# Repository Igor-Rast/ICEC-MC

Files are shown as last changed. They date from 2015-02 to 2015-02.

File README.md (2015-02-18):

# ICEC-MC
ICEC-MC Cape for BeagleBone Black

## Introduction
ICEC-MC is a project to create the plans, prototype board and software for a completly Open Source Motor Controller board in the form of a Cape that can be placed on a BeagleBone Black.
The ICEC-MC is build to fit the needs of the FirePick Delta Modular Tool system, Incorporating 4 Modular Tool headers. 
But should also be no problem to handle any other type of 3d printer or CNC machine.

## Project Status

Using Printipi (thanks Collin) the basic driver for moving the FirePickDelta is working. 
G1 commands are beeing performed correctly, G2 and a look ahead function are the next on the line to get fixed.
The calculations for the FirePick seems proven and i am now turning to the BBB for more pins so we can connect the neccecary for our project.
also an graphical user interface would be nice. 

+ idea  
- schematic / logic
- match pinouts
- board layout
- proto run
- debug

### Features

##### 4 endstop connection (x,y,z axis + Bed Level switch)
- configurable as opto or switch type(pull up)

##### 4 FirePick Delta EAT Modular Tool Headers ( new design +2p)
- new 18 pin header for EAT Modular Tool board to include Stepper VRef & BBB_ADC_GND 
- Old 16p EAT tool should work without problems, just dont populate the Termistor parts. ( wire differently)
 
##### 4 embedded DRV8825 stepper drivers (x,y,z,e)
- Digital Current Control (DAC088S085)
- All DRV8825 stepping modes (full step, half step, 1/4 step, 1/8 step, 1/16 step, 1/32 step).,

##### 4 steppers connection tru Modular Tool Header (one tool at a time)
- Digital Current Control (DAC088S085) (if new EAT tool used)

##### 7 BBB ADC inputs for thermistor 
- 3 on board
- 4 accessable tru Modular Tool Headers

##### 4 Servo connections 
- connect up to 4 servos or ledstrips

##### E-Stop Logic Circuit (Oh shit, Button)
- deactivate all steppers and tools with the push of a button.

##### Imbedded voltage regulators
- 12V step down --> fans , if using 24V on motors
- 5C step down --> beaglebone black and logic

##### I2C controlled standalone PWM controller (PCA9685PW)  
- 3 Enbedded Hi-Power Mosfest (AON6758) e.g. heatbed/hotend/vacuumpump
- 3 Embedded Low-Power Mosfet (NIF5002) e.g. fan/leds
- 4 PWM control of D_Out on Modular Tool Headers
- 6 PWM signals left unused (break these out?/add some status leds?)

##### 40pin Connection for Graphical Interface Expansion using cheap 4.3inch 3.2 TFT LCD modules 
- ssd1962 display driver 
- touch sensor 
- sd card reader

##### Remote on function for ATX powersupply
- turn the ATX PSU on/off using the M81/M82 (single ATX supply)

##### BBB reset button

## Developers
TODO: setup google group
If you'd like to be involved in the development of ICEC-MC, please PM me.

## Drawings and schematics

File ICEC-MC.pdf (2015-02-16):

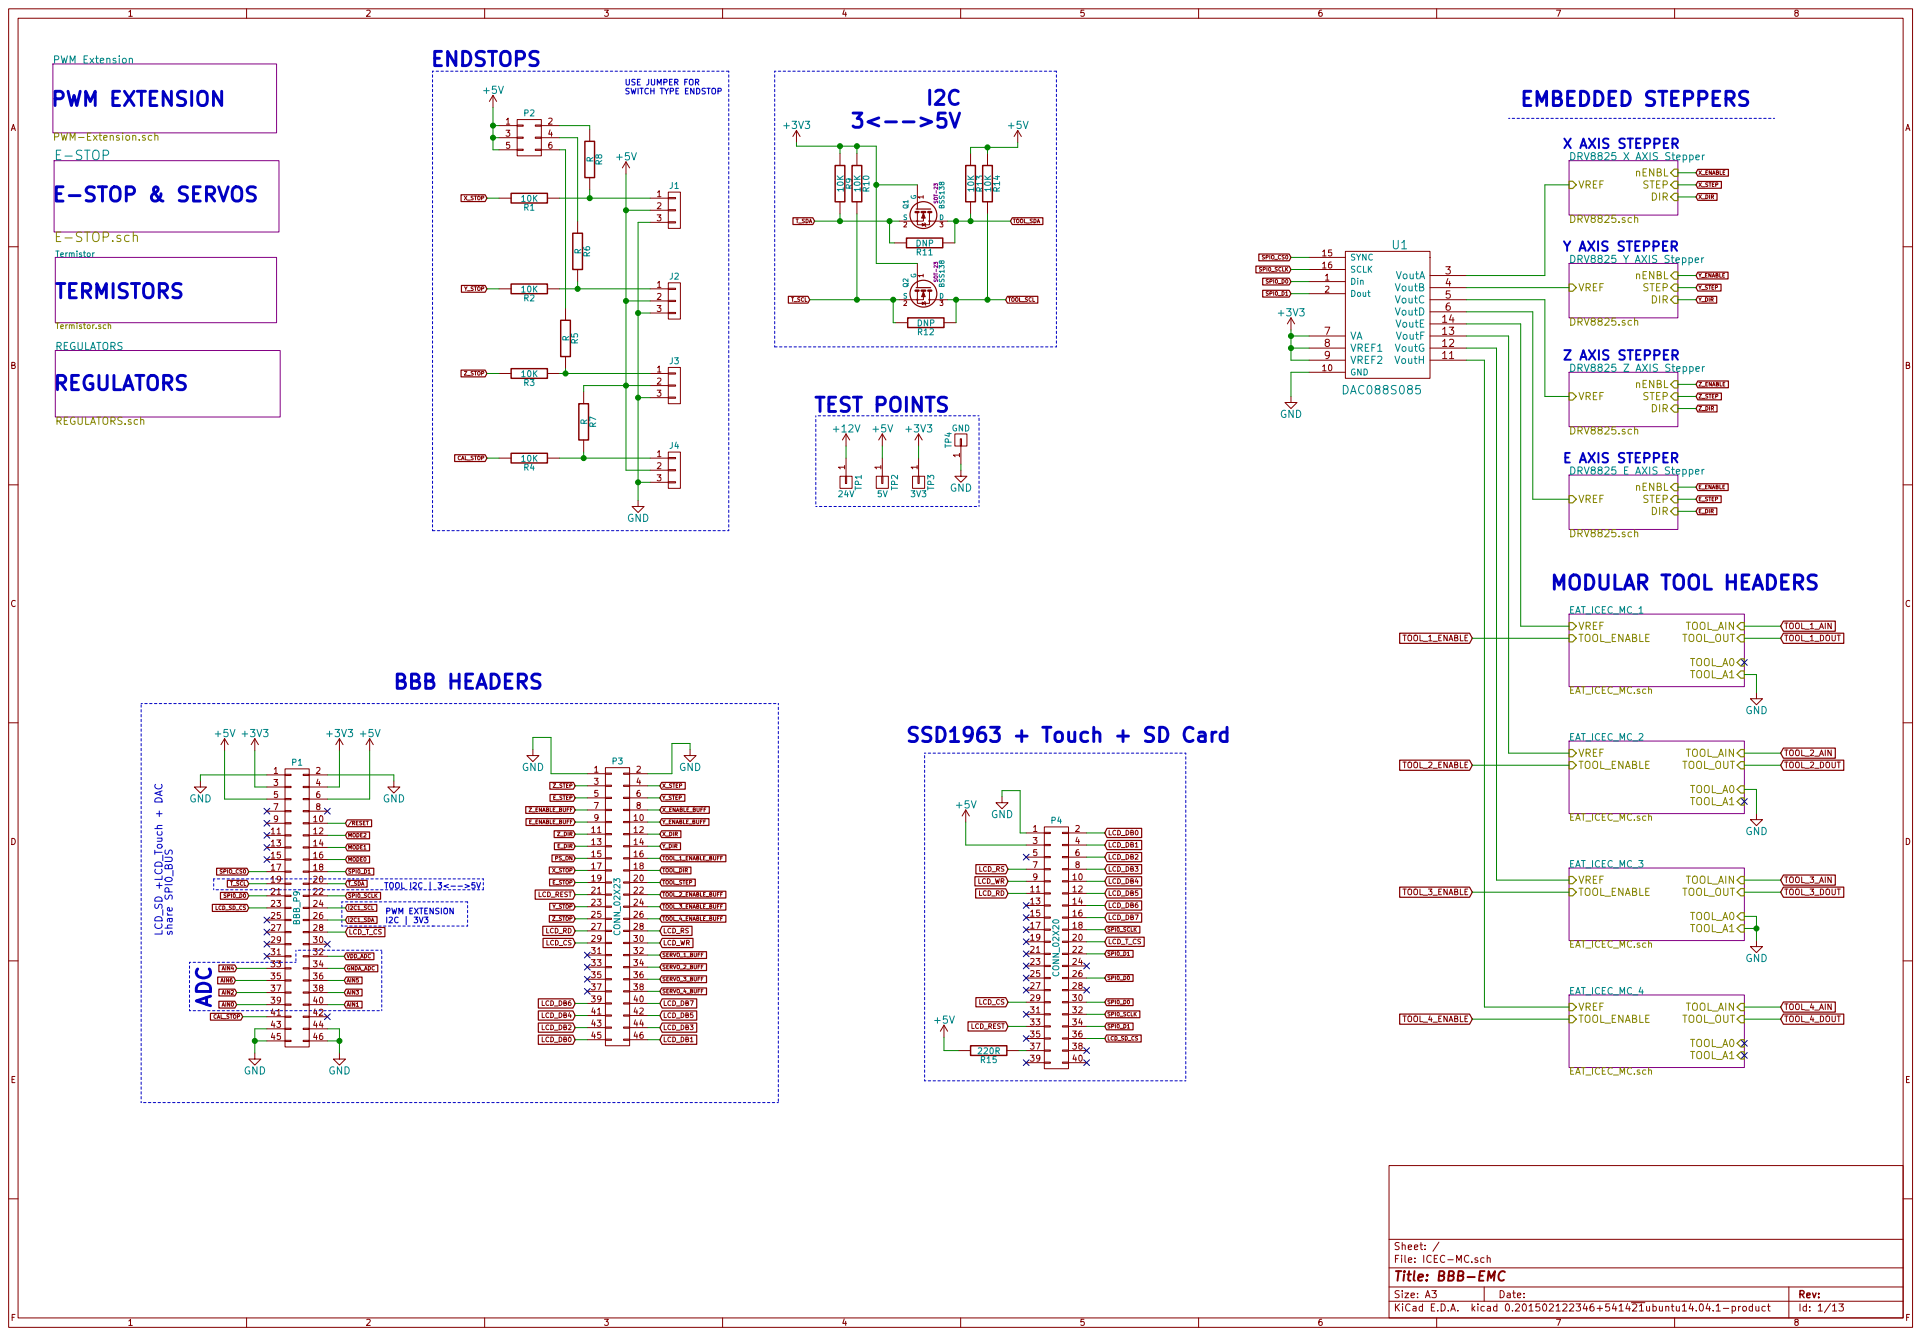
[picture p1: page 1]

PWM Extension PWM-Extension.sch

DRV8825 X AXIS Stepper DRV8825.sch STEP DIR | nENBL VREF

Y AXIS STEPPER
DRV8825 Y AXIS Stepper DRV8825.sch STEP DIR
nENBL VREF Z AXIS STEPPER

DRV8825 Z AXIS Stepper DRV8825.sch STEP DIR
nENBL VREF E AXIS STEPPER

REGULATORS

DRV8825 E AXIS Stepper DRV8825.sch STEP DIR
nENBL VREF

File: ICEC-MC.sch Sheet: /
Id: 1/13 Title: BBB-EMC

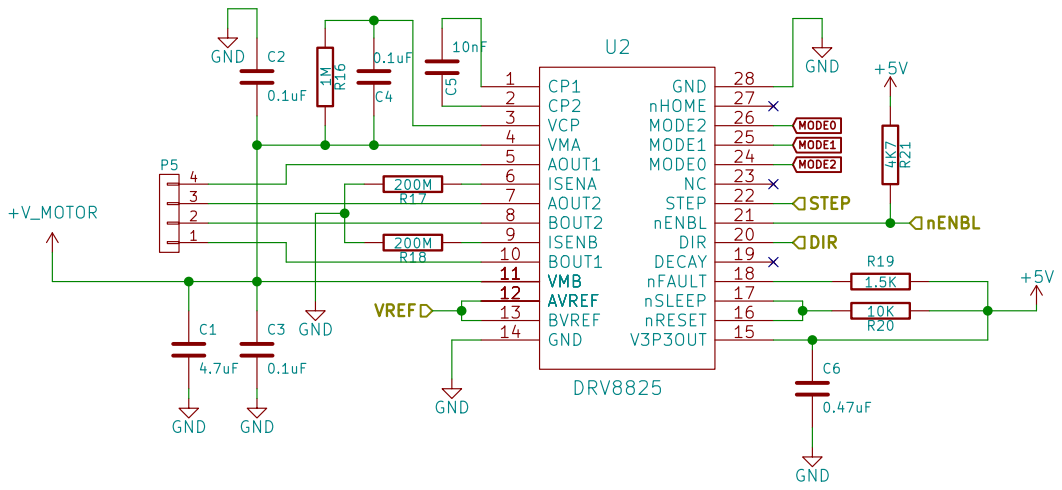
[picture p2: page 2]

MODE0 MODE1 MODE2 +V_MOTOR

File: DRV8825.sch Sheet: /DRV8825 X AXIS Stepper/
Id: 2/13 Title: DRV8825 Stepper -| ADC-->VRF

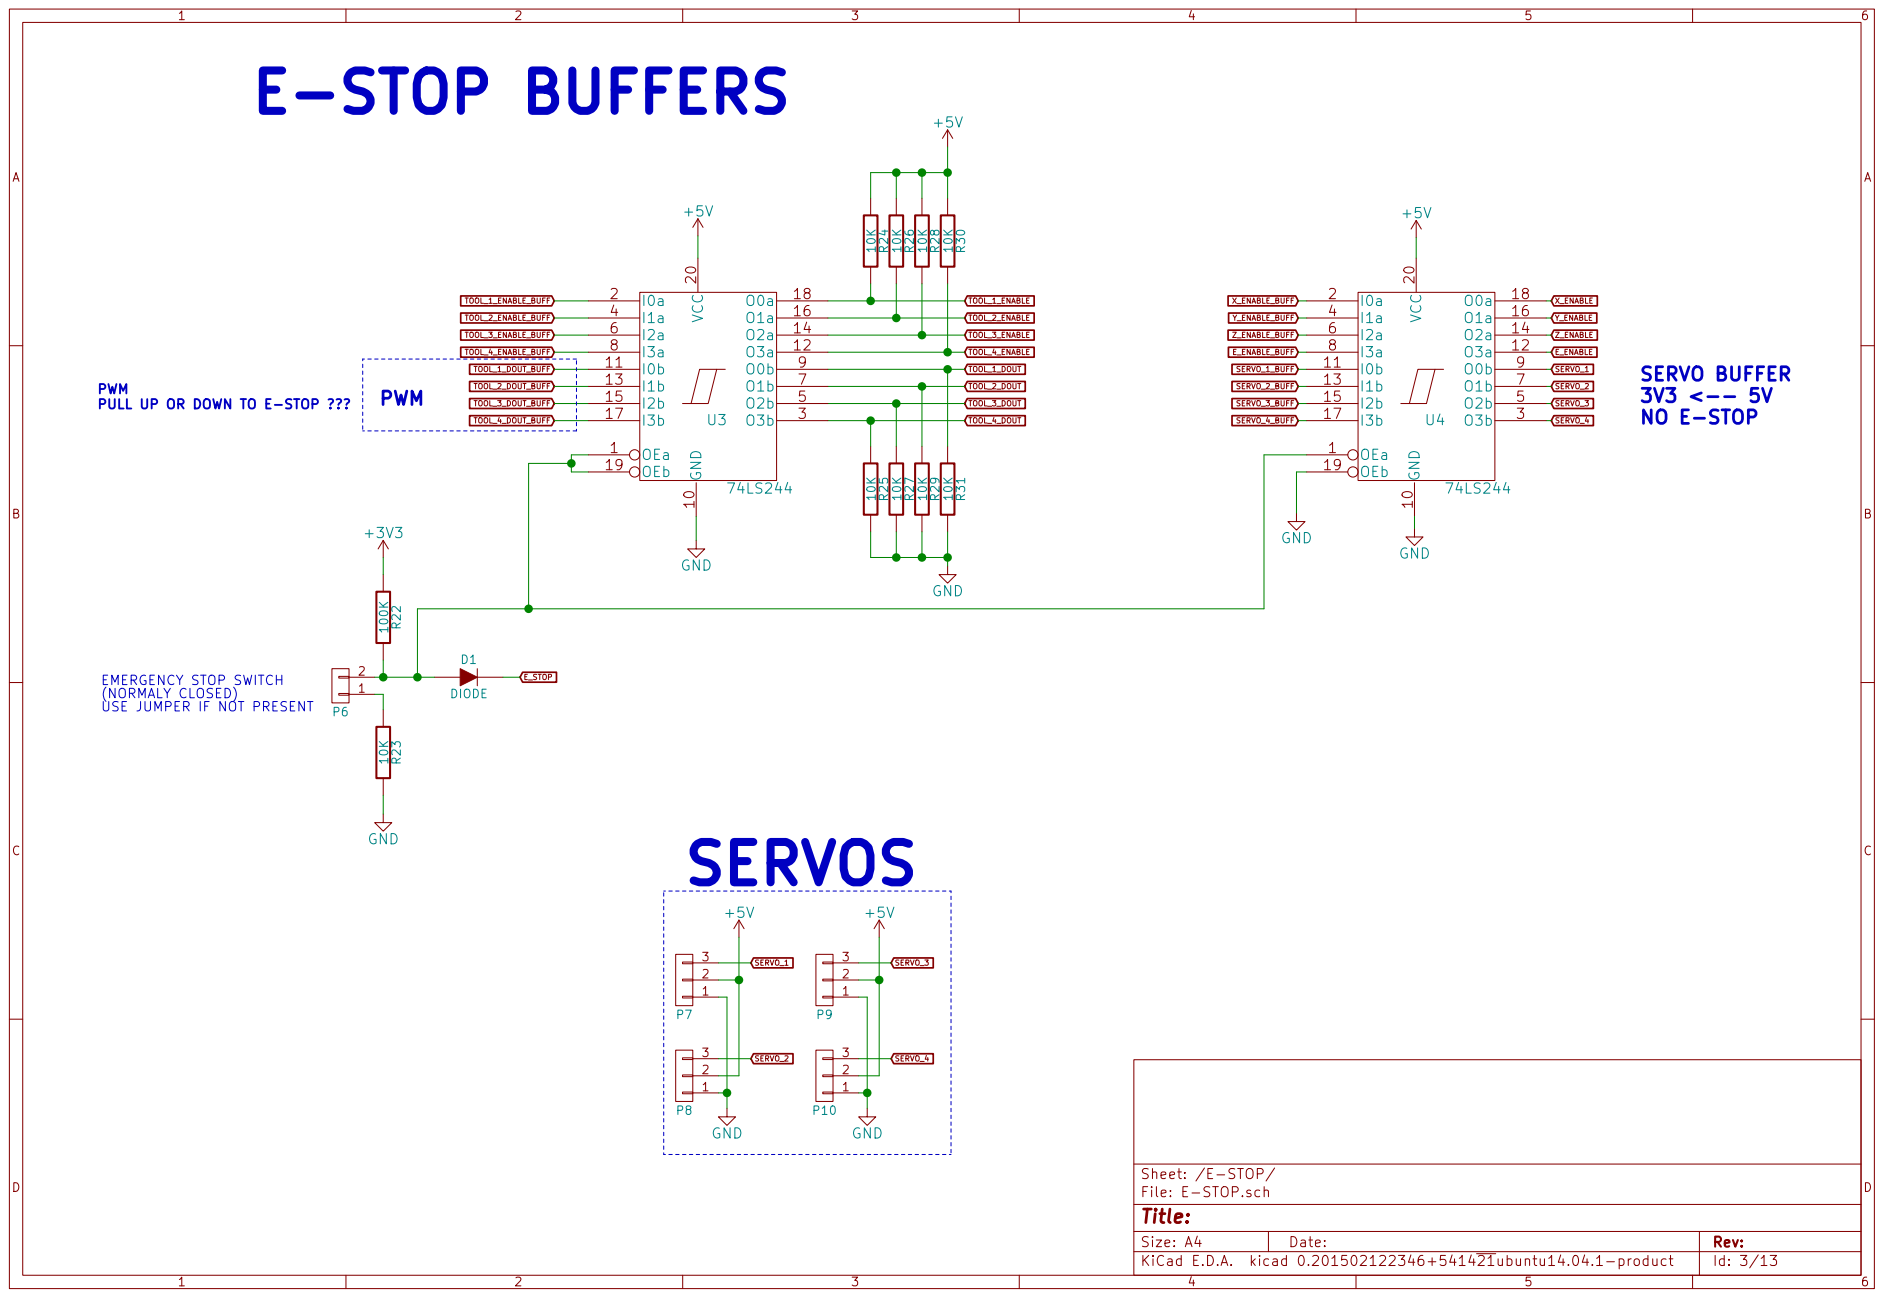
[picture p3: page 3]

Id: 3/13 Title: File: E-STOP.sch Sheet: /E-STOP/

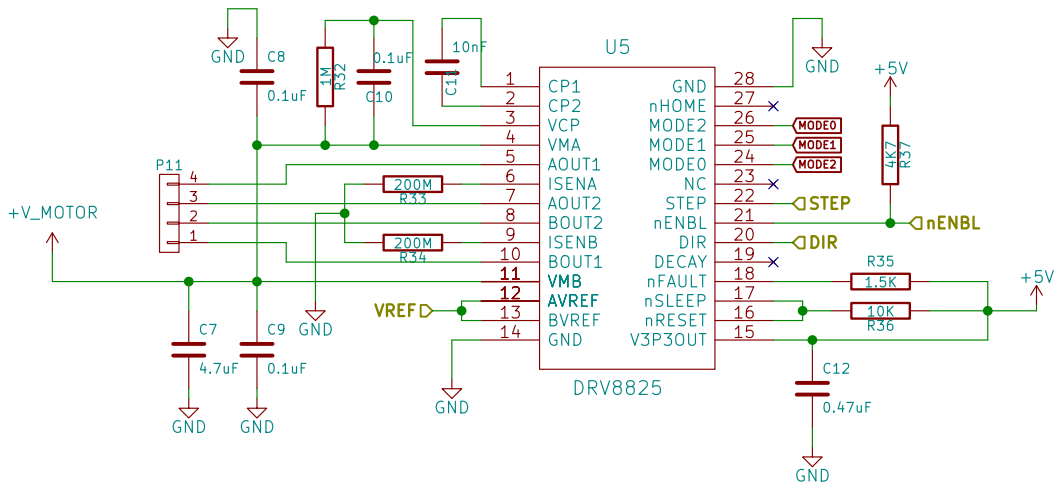
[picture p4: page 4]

MODE0 MODE1 MODE2 +V_MOTOR

File: DRV8825.sch Sheet: /DRV8825 Y AXIS Stepper/
Id: 4/13 Title: DRV8825 Stepper -| ADC-->VRF

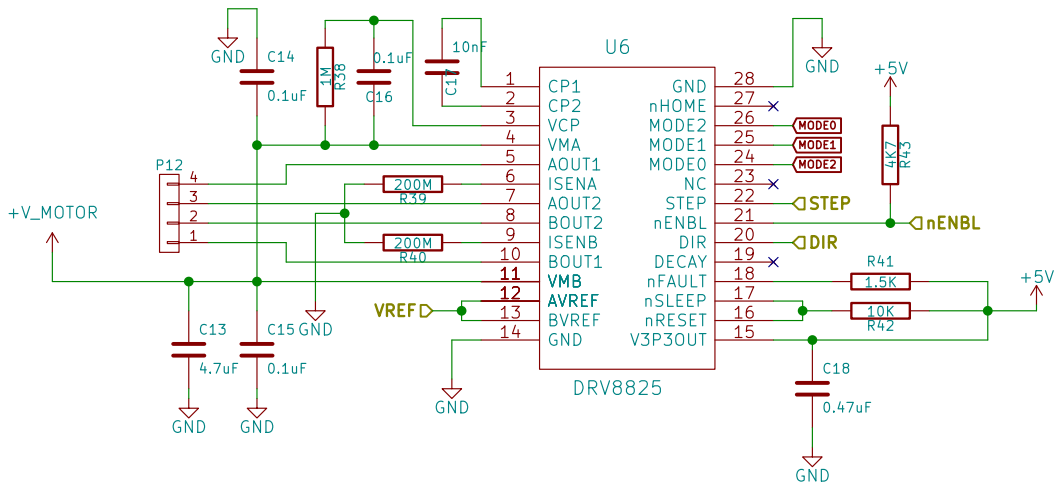
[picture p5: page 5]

MODE0 MODE1 MODE2 +V_MOTOR

File: DRV8825.sch Sheet: /DRV8825 Z AXIS Stepper/
Id: 5/13 Title: DRV8825 Stepper -| ADC-->VRF

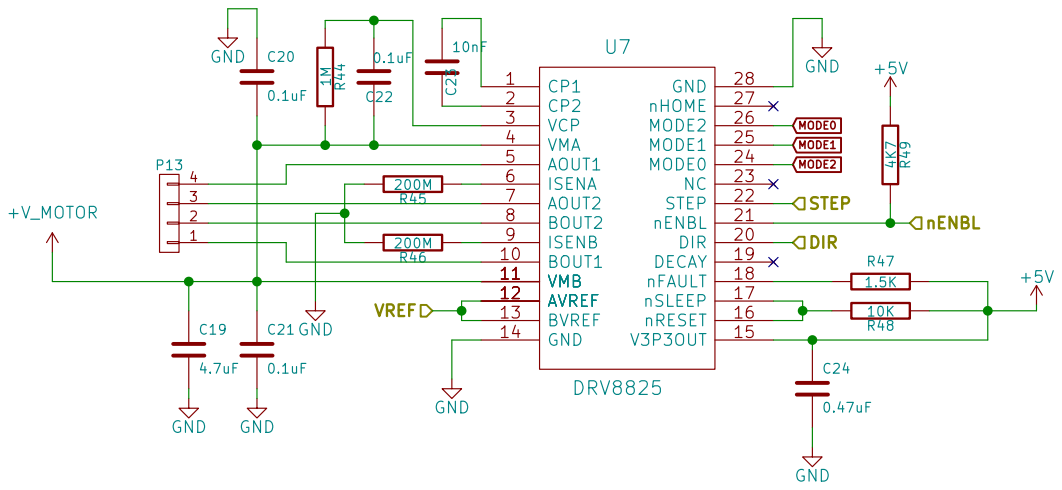
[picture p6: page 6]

MODE0 MODE1 MODE2 +V_MOTOR

File: DRV8825.sch Sheet: /DRV8825 E AXIS Stepper/
Id: 6/13 Title: DRV8825 Stepper -| ADC-->VRF

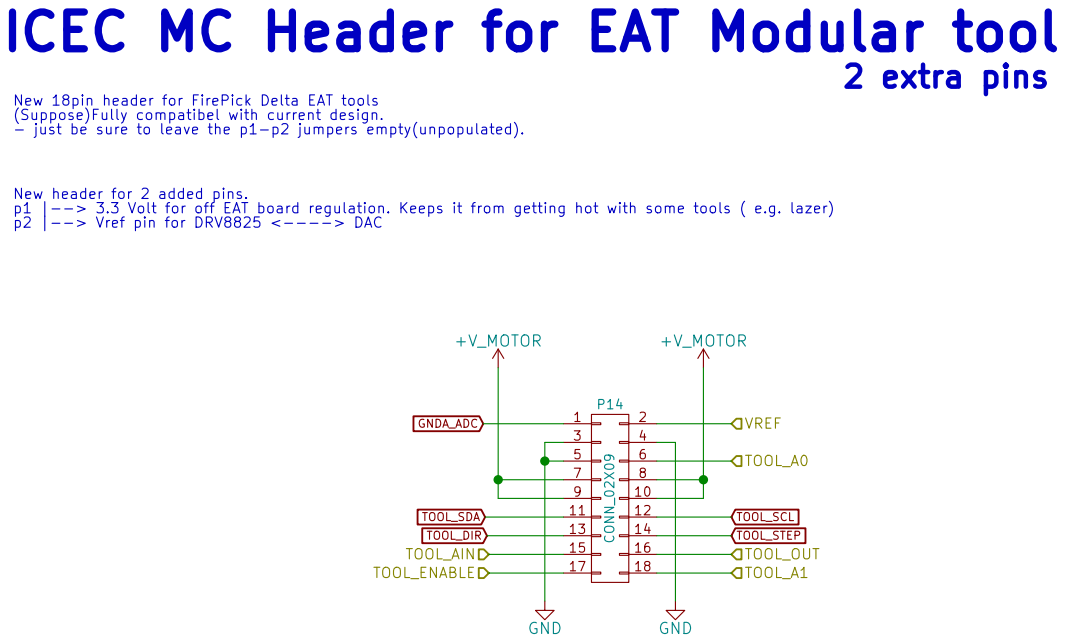
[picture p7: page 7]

ICEC MC Header for EAT Modular tool

TOOL_A1 VREF New 18pin header for FirePick Delta EAT tools
(Suppose)Fully compatibel with current design.
- just be sure to leave the p1-p2 jumpers empty(unpopulated).

New header for 2 added pins.
p1 |--> 3.3 Volt for off EAT board regulation. Keeps it from getting hot with some tools ( e.g. lazer)
p2 |--> Vref pin for DRV8825 <----> DAC

Sheet: /EAT_ICEC_MC_1/
File: EAT_ICEC_MC.sch
Id: 7/13 Title: ICEC MC EAT HEADER

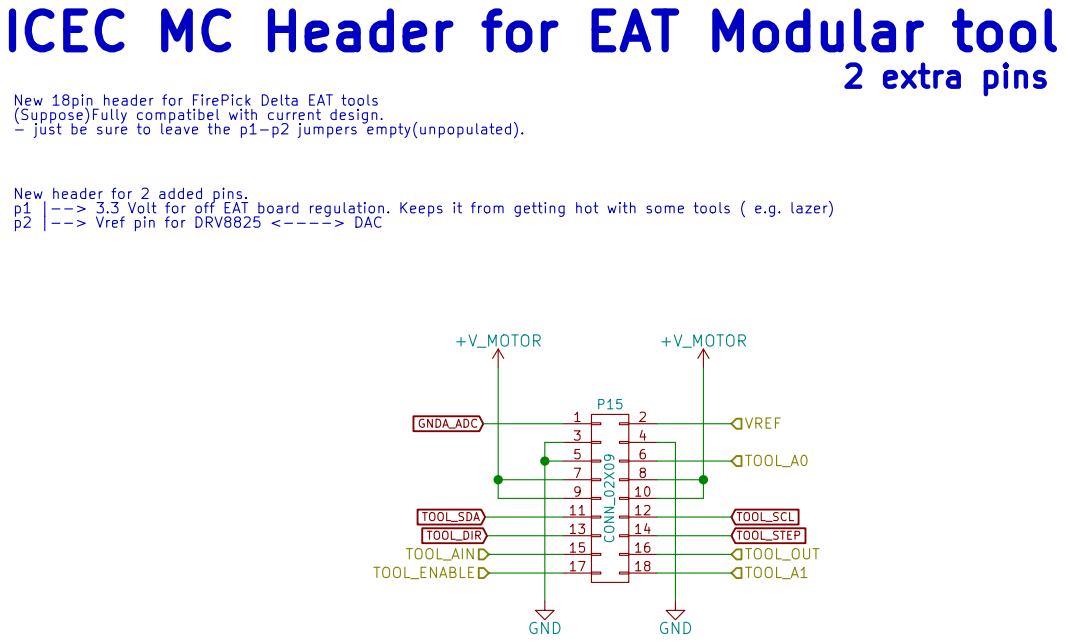
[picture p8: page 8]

ICEC MC Header for EAT Modular tool

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

Sheet: /EAT_ICEC_MC_2/
File: EAT_ICEC_MC.sch
Id: 8/13 Title: ICEC MC EAT HEADER

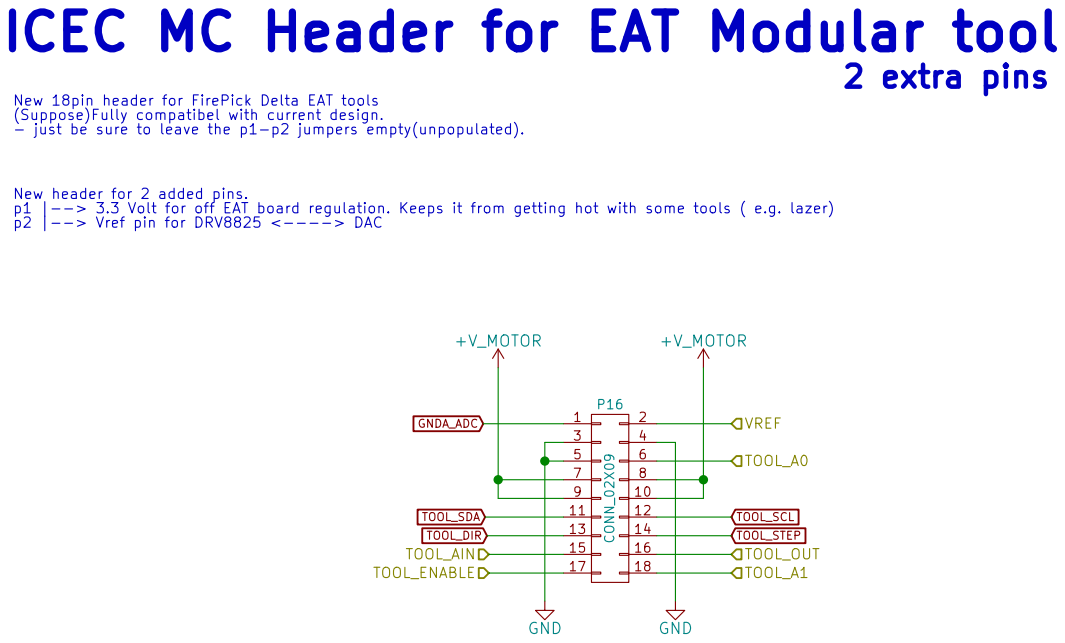
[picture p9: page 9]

ICEC MC Header for EAT Modular tool

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

Sheet: /EAT_ICEC_MC_3/
File: EAT_ICEC_MC.sch
Id: 9/13 Title: ICEC MC EAT HEADER

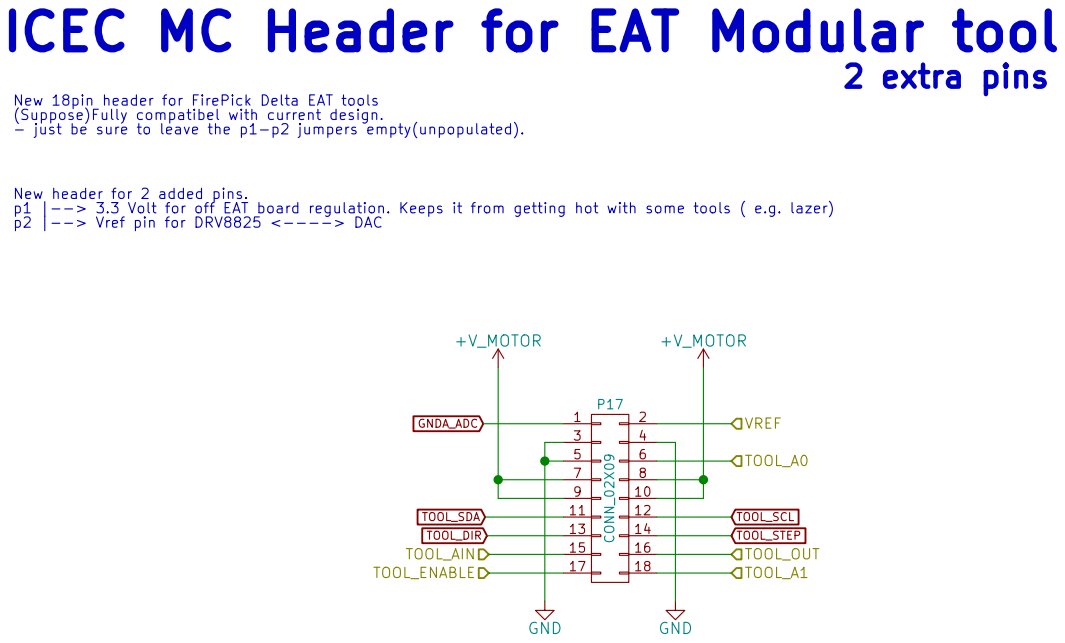
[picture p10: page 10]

ICEC MC Header for EAT Modular tool

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

Sheet: /EAT_ICEC_MC_4/
File: EAT_ICEC_MC.sch
Id: 10/13 Title: ICEC MC EAT HEADER

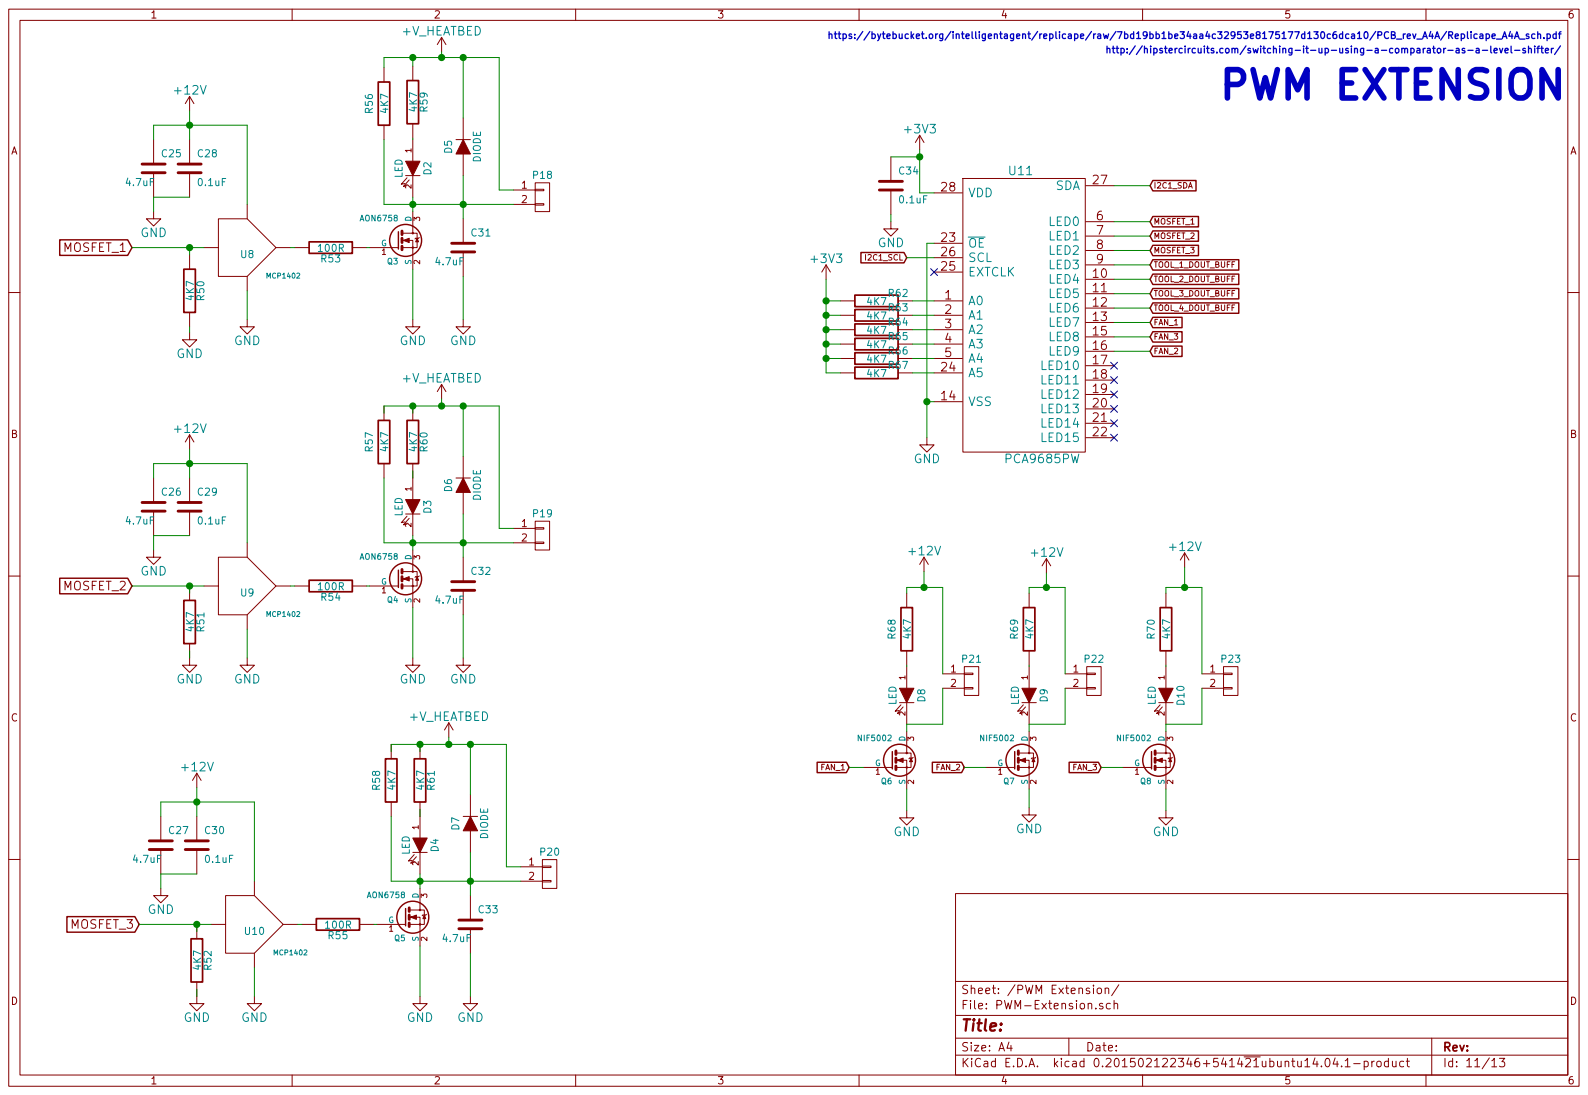
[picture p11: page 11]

TOOL_4_DOUT_BUFF https://bytebucket.org/intelligentagent/replicape/raw/7bd19bb1be34aa4c32953e8175177d130c6dca10/PCB_rev_A4A/Replicape_A4A_sch.pdf

Id: 11/13 Title: File: PWM-Extension.sch Sheet: /PWM Extension/

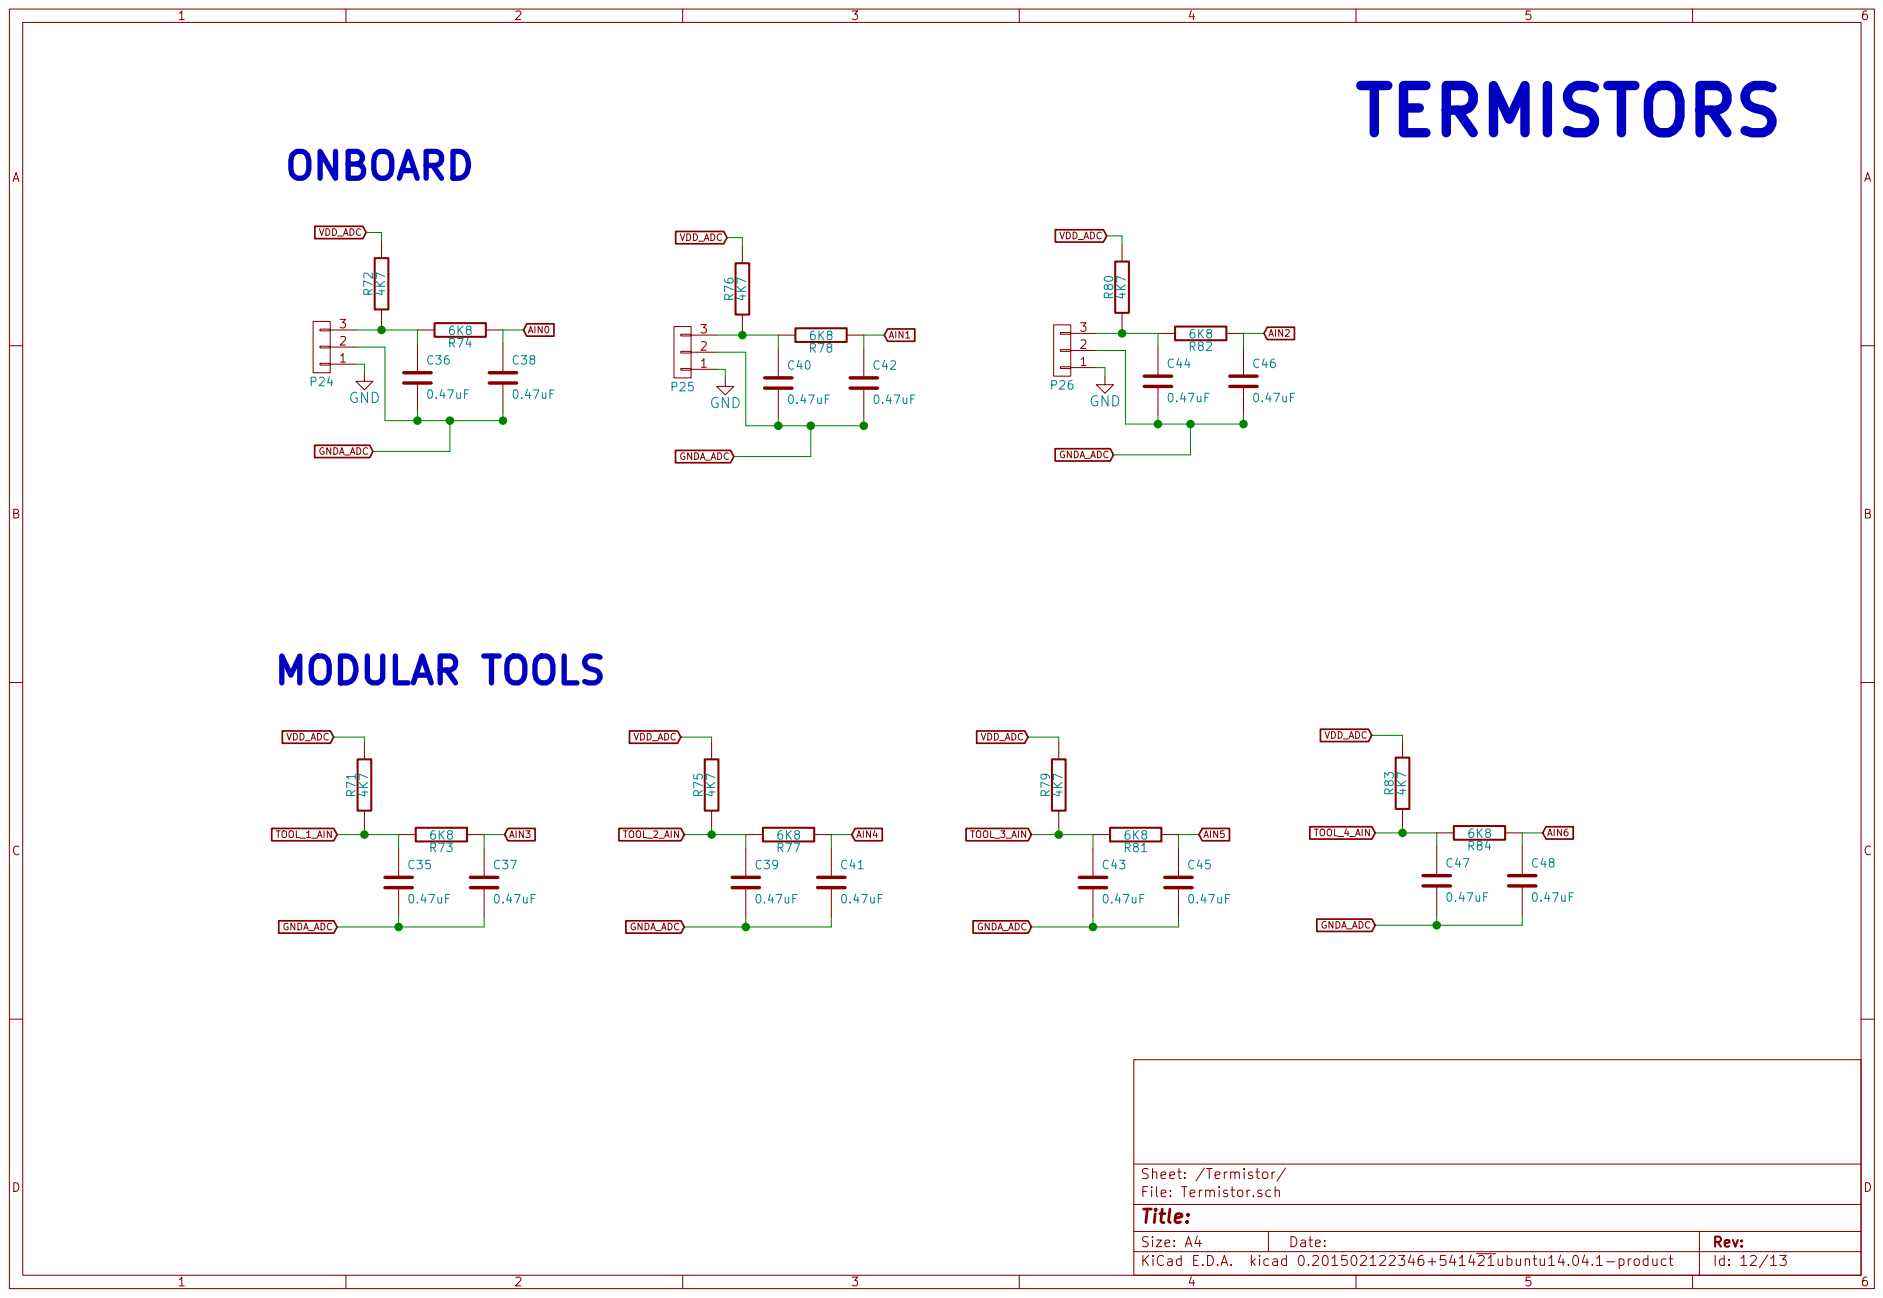
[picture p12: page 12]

Id: 12/13 Title: File: Termistor.sch Sheet: /Termistor/


REMOTE ATX POWER INPUTS

SHORT FOR SINGLE PSU HEATBED ONLY:
BBB RESET SGND

4 VFB 5 PG 8 EN 9 BOOT 10 EP 17 VIN 2*3* PGND 14*1 SW 1*12 U12

Id: 13/13 Title: File: REGULATORS.sch Sheet: /REGULATORS/

STEP DOWN CONVERTERS TAKEN FROM REPLICAPE

https://bytebucket.org/intelligentagent/replicape/raw/7bd19bb1be34aa4c32953e8175177d130c6dca10/PCB_rev_A4A/Replicape_A4A_sch.pdf

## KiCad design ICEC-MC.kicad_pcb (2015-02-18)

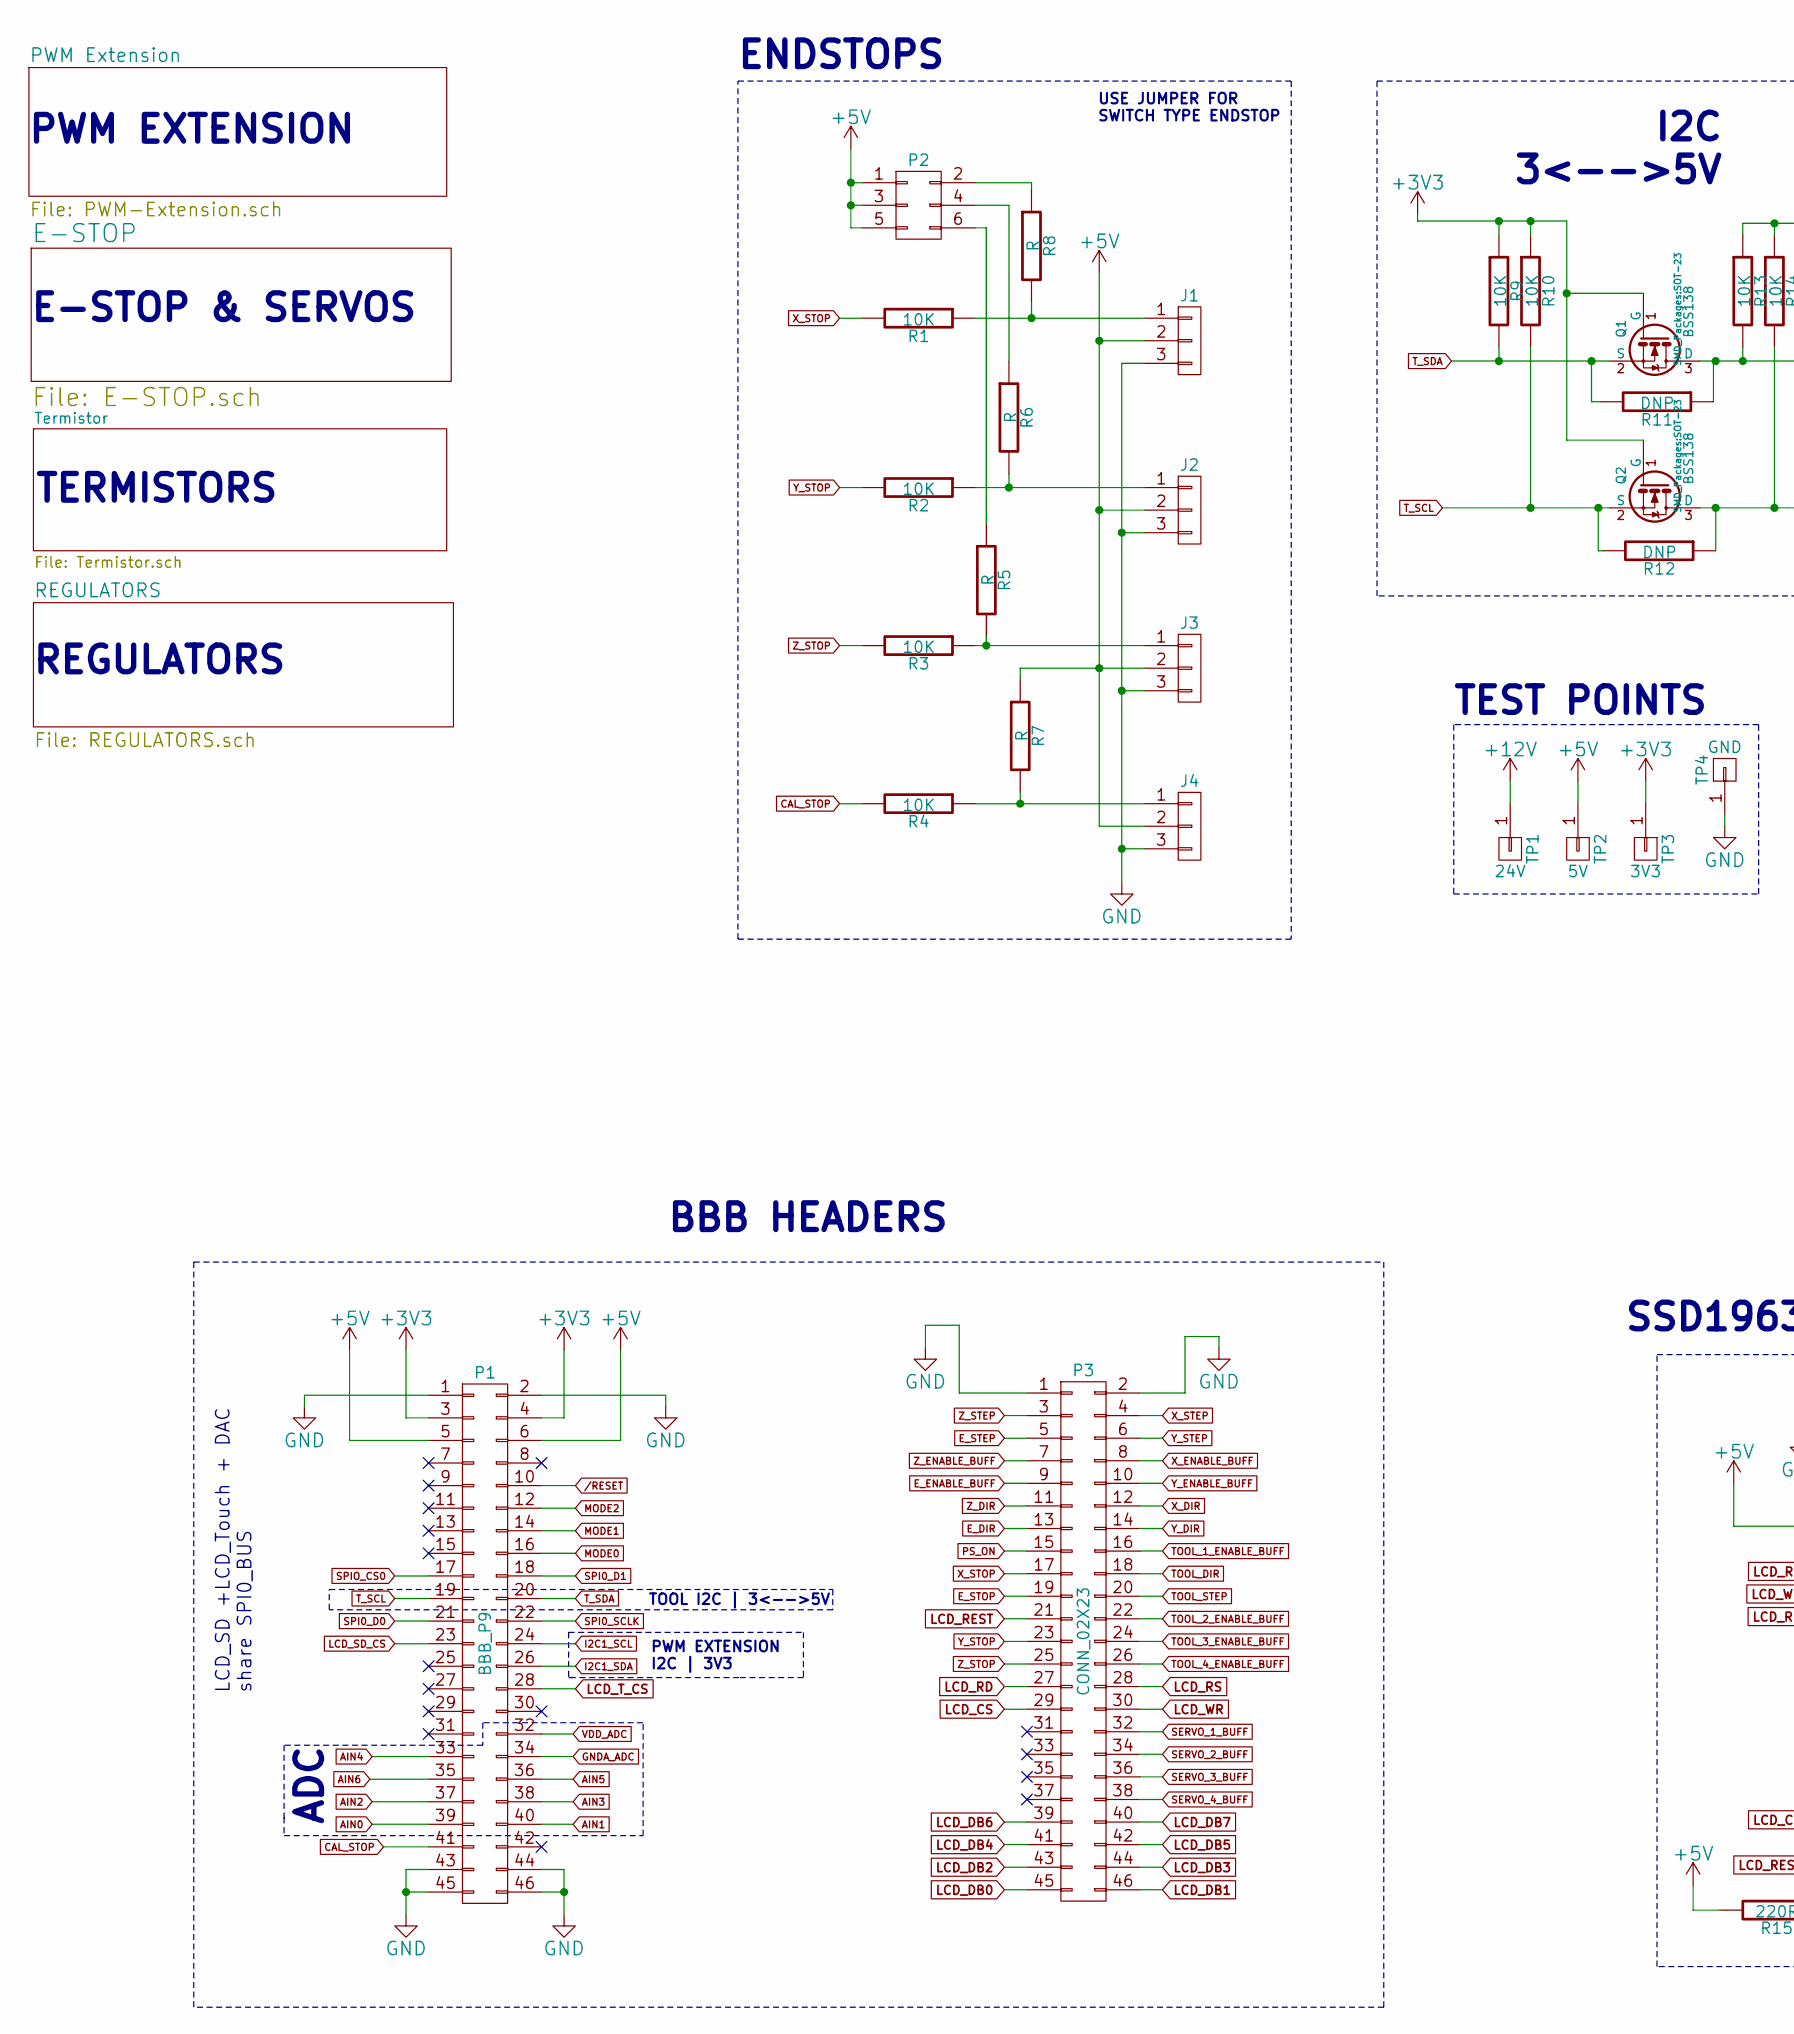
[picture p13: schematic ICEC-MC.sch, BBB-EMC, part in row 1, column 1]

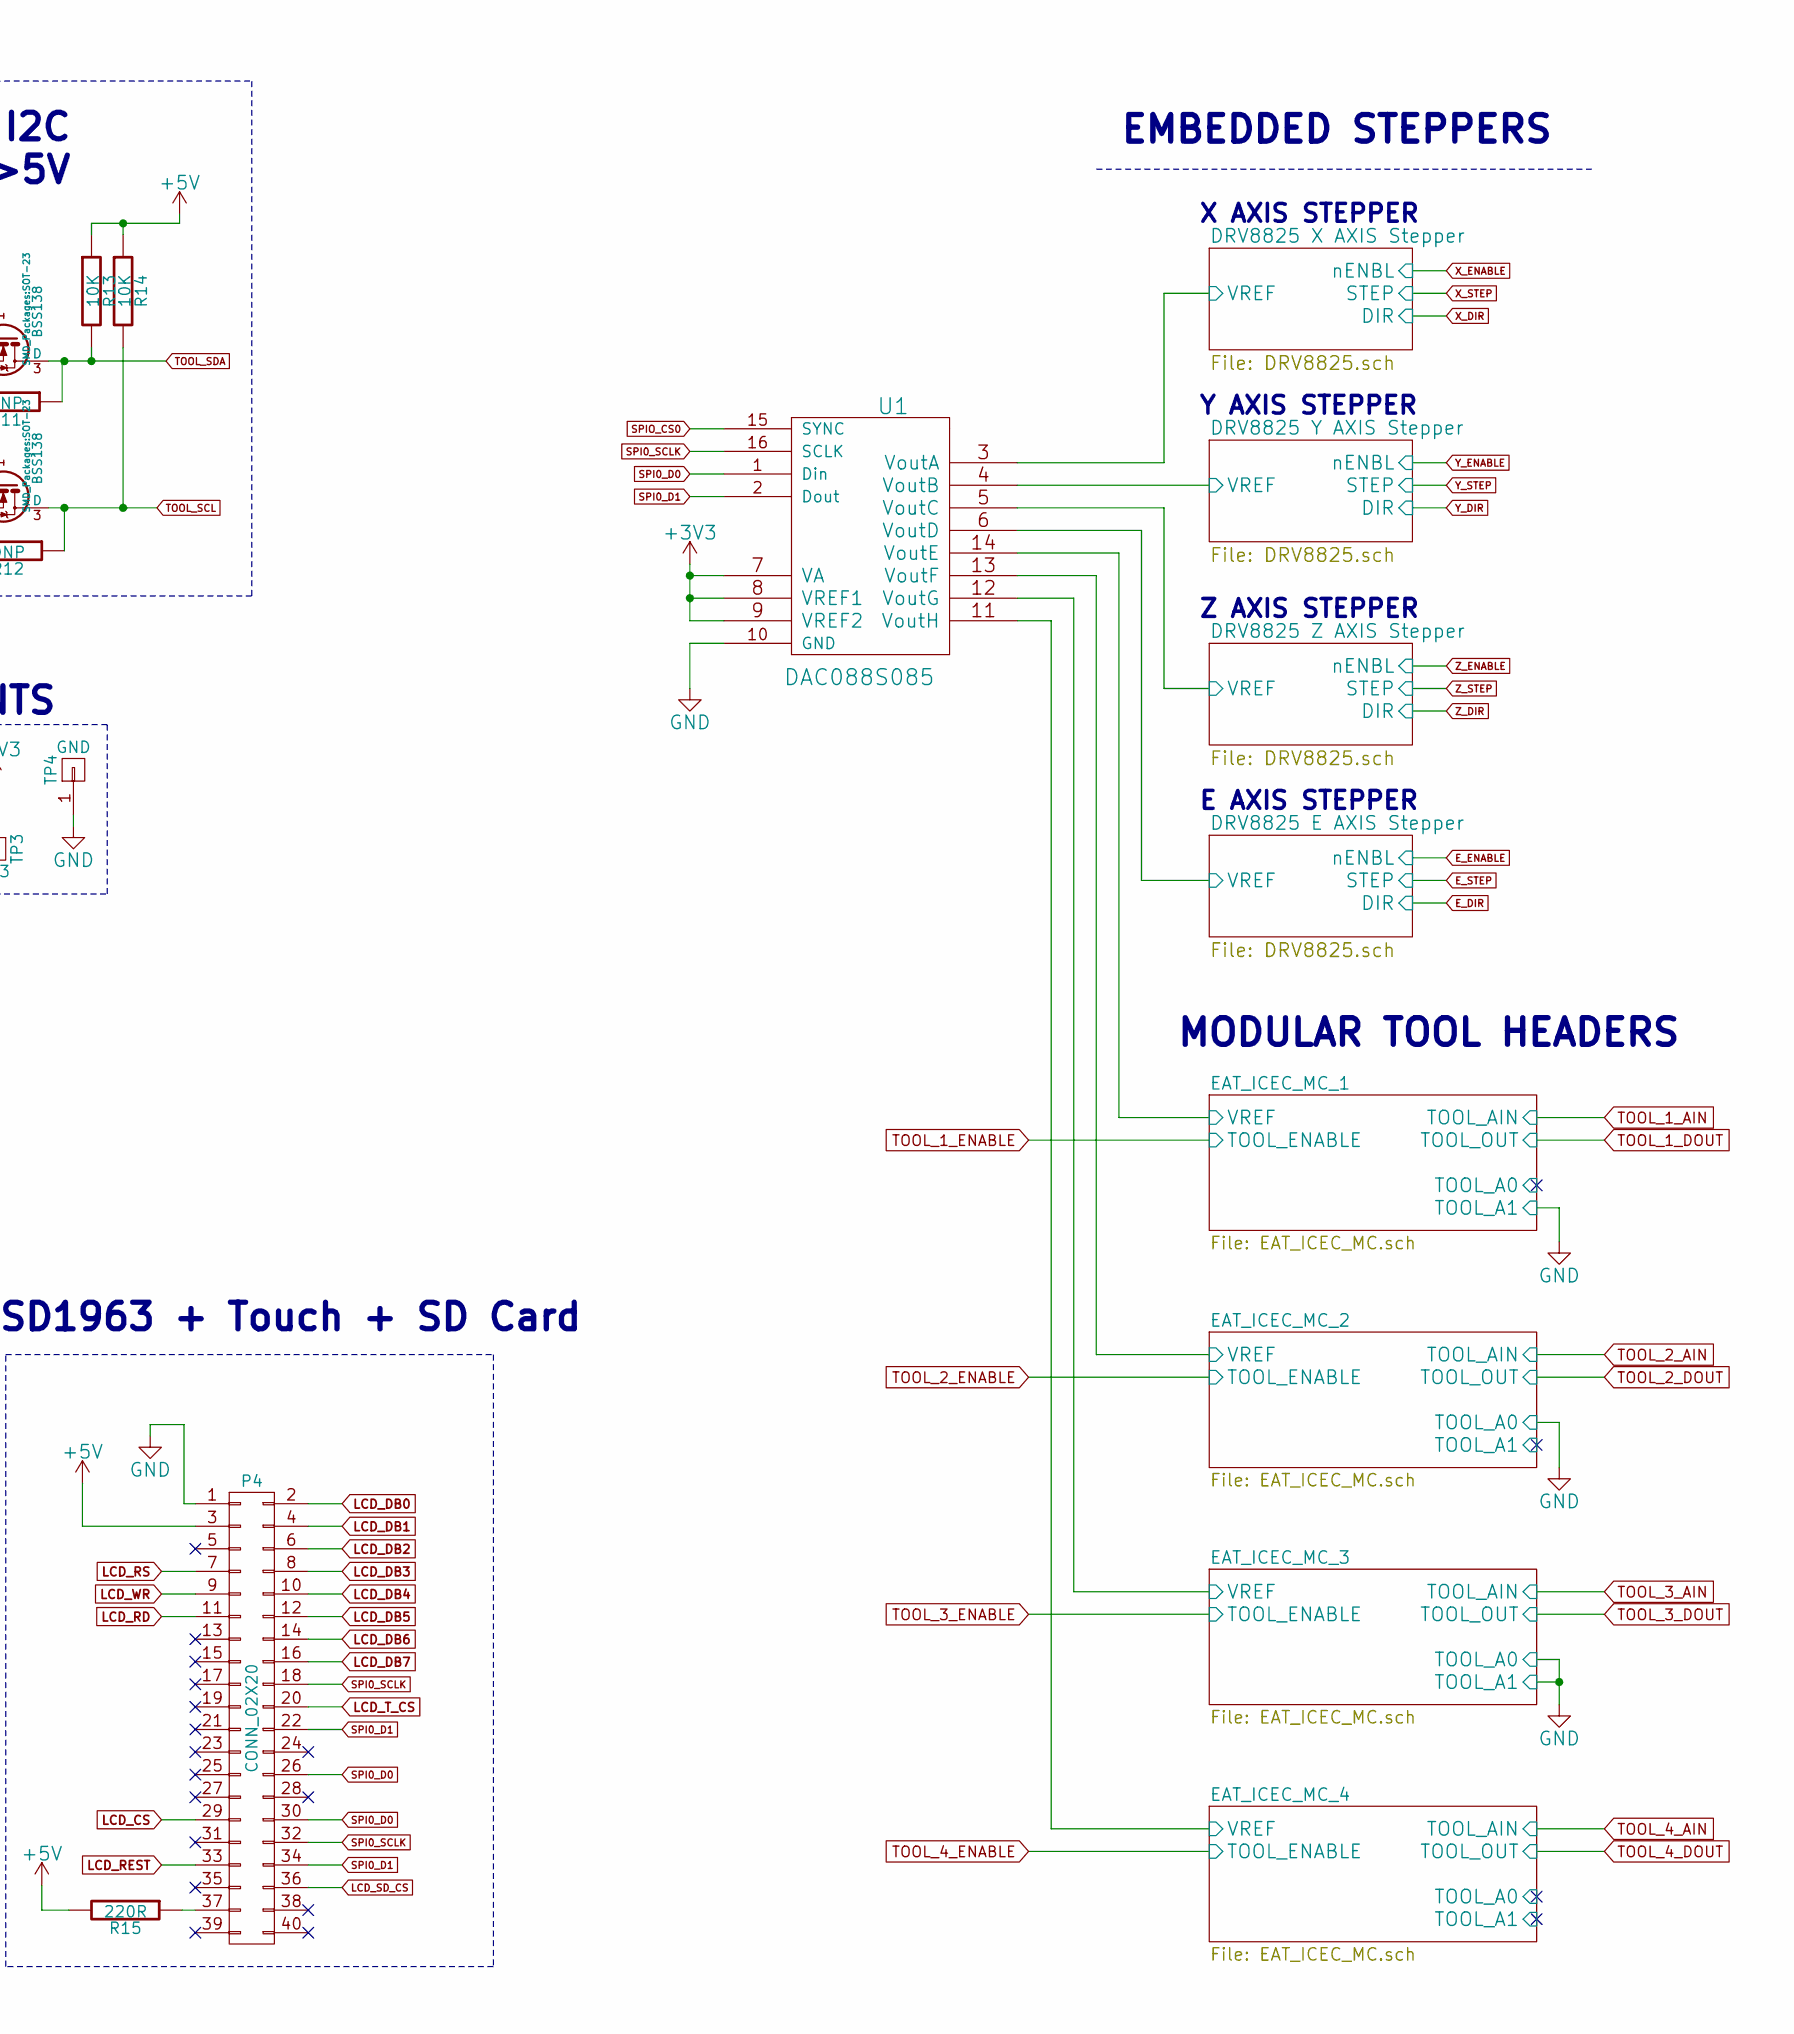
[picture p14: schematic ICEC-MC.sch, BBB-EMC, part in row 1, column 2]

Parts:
J1, J2, J3, J4: CONN_01X03; Socket_Strip_Straight_1x03
P1: BBB_P9; Socket_Strip_Straight_2x23
P2: CONN_02X03; Socket_Strip_Straight_2x03
P3: CONN_02X23; Socket_Strip_Straight_2x23
P4: CONN_02X20; Socket_Strip_Straight_2x20
Q1, Q2: BSS138; SOT-23
R1, R2, R3, R4, R9, R10, R13, R14: 10K; R_0805_HandSoldering
R5, R6, R7, R8: R; R_0805_HandSoldering
R11, R12: DNP; R_0805_HandSoldering
R15: 220R; R_0805_HandSoldering
TP1: 24V; Pin_Header_Straight_1x01
TP2: 5V; Pin_Header_Straight_1x01
TP3: 3V3; Pin_Header_Straight_1x01
TP4: GND; Pin_Header_Straight_1x01
U1: DAC088S085; TSSOP-16_4.4x5mm_Pitch0.65mm

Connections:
+3V3: P1.3, P1.4, Q1.1 (G), Q2.1 (G), R9.1, R10.1, TP3.1, U1.7 (VA), U1.8 (VREF1), U1.9 (VREF2); also elsewhere on the board
+5V: J1.2, J2.2, J3.2, J4.2, P1.5, P1.6, P2.1, P2.3, P2.5, P4.3, R7.1, R13.1, R14.1, R15.2, TP2.1; also elsewhere on the board
/DRV8825 E AXIS Stepper/VREF: U1.6 (VoutD); also elsewhere on the board
/DRV8825 X AXIS Stepper/VREF: U1.3 (VoutA); also elsewhere on the board
/DRV8825 Y AXIS Stepper/VREF: U1.4 (VoutB); also elsewhere on the board
/DRV8825 Z AXIS Stepper/VREF: U1.5 (VoutC); also elsewhere on the board
/EAT_ICEC_MC_1/VREF: U1.14 (VoutE); also elsewhere on the board
/EAT_ICEC_MC_2/VREF: U1.13 (VoutF); also elsewhere on the board
/EAT_ICEC_MC_3/VREF: U1.12 (VoutG); also elsewhere on the board
/EAT_ICEC_MC_4/VREF: U1.11 (VoutH); also elsewhere on the board
/RESET: P1.10
AIN0: P1.39; also elsewhere on the board
AIN1: P1.40; also elsewhere on the board
AIN2: P1.37; also elsewhere on the board
AIN3: P1.38; also elsewhere on the board
AIN4: P1.33; also elsewhere on the board
AIN5: P1.36; also elsewhere on the board
AIN6: P1.35; also elsewhere on the board
CAL_STOP: P1.41, R4.2
E_DIR: P3.13; also elsewhere on the board
E_ENABLE_BUFF: P3.9; also elsewhere on the board
E_STEP: P3.5; also elsewhere on the board
E_STOP: P3.19
GNDA_ADC: P1.34; also elsewhere on the board
I2C1_SCL: P1.24; also elsewhere on the board
I2C1_SDA: P1.26; also elsewhere on the board
LCD_CS: P3.29, P4.29
LCD_DB0: P3.45, P4.2
LCD_DB1: P3.46, P4.4
LCD_DB2: P3.43, P4.6
LCD_DB3: P3.44, P4.8
LCD_DB4: P3.41, P4.10
LCD_DB5: P3.42, P4.12
LCD_DB6: P3.39, P4.14
LCD_DB7: P3.40, P4.16
LCD_RD: P3.27, P4.11
LCD_REST: P3.21, P4.33
LCD_RS: P3.28, P4.7
LCD_SD_CS: P1.23, P4.36
LCD_T_CS: P1.28, P4.20
LCD_WR: P3.30, P4.9
MODE0: P1.16; also elsewhere on the board
MODE1: P1.14; also elsewhere on the board
MODE2: P1.12; also elsewhere on the board
unnamed: J1.1, R1.1, R8.2
unnamed: J2.1, R2.1, R6.2
unnamed: J3.1, R3.1, R5.2
unnamed: J4.1, R4.1, R7.2
unnamed: P2.2, R8.1
unnamed: P2.4, R6.1
unnamed: P2.6, R5.1
unnamed: P4.37, R15.1
PS_ON: P3.15; also elsewhere on the board
SERVO_1_BUFF: P3.32; also elsewhere on the board
SERVO_2_BUFF: P3.34; also elsewhere on the board
SERVO_3_BUFF: P3.36; also elsewhere on the board
SERVO_4_BUFF: P3.38; also elsewhere on the board
SPI0_D0: P1.21, P4.26, P4.30, U1.1 (Din)
SPI0_D1: P1.18, P4.22, P4.34, U1.2 (Dout)
SPI0_SCLK: P1.22, P4.18, P4.32, U1.16 (SCLK)
SPIO_CS0: P1.17, U1.15 (SYNC)
TOOL_1_ENABLE_BUFF: P3.16; also elsewhere on the board
TOOL_2_ENABLE_BUFF: P3.22; also elsewhere on the board
TOOL_3_ENABLE_BUFF: P3.24; also elsewhere on the board
TOOL_4_ENABLE_BUFF: P3.26; also elsewhere on the board
TOOL_DIR: P3.18; also elsewhere on the board
TOOL_SCL: Q2.3 (D), R12.1, R14.2; also elsewhere on the board
TOOL_SDA: Q1.3 (D), R11.1, R13.2; also elsewhere on the board
TOOL_STEP: P3.20; also elsewhere on the board
T_SCL: P1.19, Q2.2 (S), R10.2, R12.2
T_SDA: P1.20, Q1.2 (S), R9.2, R11.2
VDD_ADC: P1.32; also elsewhere on the board
X_DIR: P3.12; also elsewhere on the board
X_ENABLE_BUFF: P3.8; also elsewhere on the board
X_STEP: P3.4; also elsewhere on the board
X_STOP: P3.17, R1.2
Y_DIR: P3.14; also elsewhere on the board
Y_ENABLE_BUFF: P3.10; also elsewhere on the board
Y_STEP: P3.6; also elsewhere on the board
Y_STOP: P3.23, R2.2
Z_DIR: P3.11; also elsewhere on the board
Z_ENABLE_BUFF: P3.7; also elsewhere on the board
Z_STEP: P3.3; also elsewhere on the board
Z_STOP: P3.25, R3.2

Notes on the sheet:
ENDSTOPS
X AXIS STEPPER
Y AXIS STEPPER
EMBEDDED STEPPERS
Z AXIS STEPPER
E AXIS STEPPER
E-STOP & SERVOS
MODULAR TOOL HEADERS
SSD1963 + Touch + SD Card
LCD_SD +LCD_Touch + DAC share SPI0_BUS
BBB HEADERS
TOOL I2C | 3<-->5V
PWM EXTENSION
USE JUMPER FOR SWITCH TYPE ENDSTOP
ADC
TERMISTORS
I2C 3<-->5V
REGULATORS
TEST POINTS
PWM EXTENSION I2C | 3V3

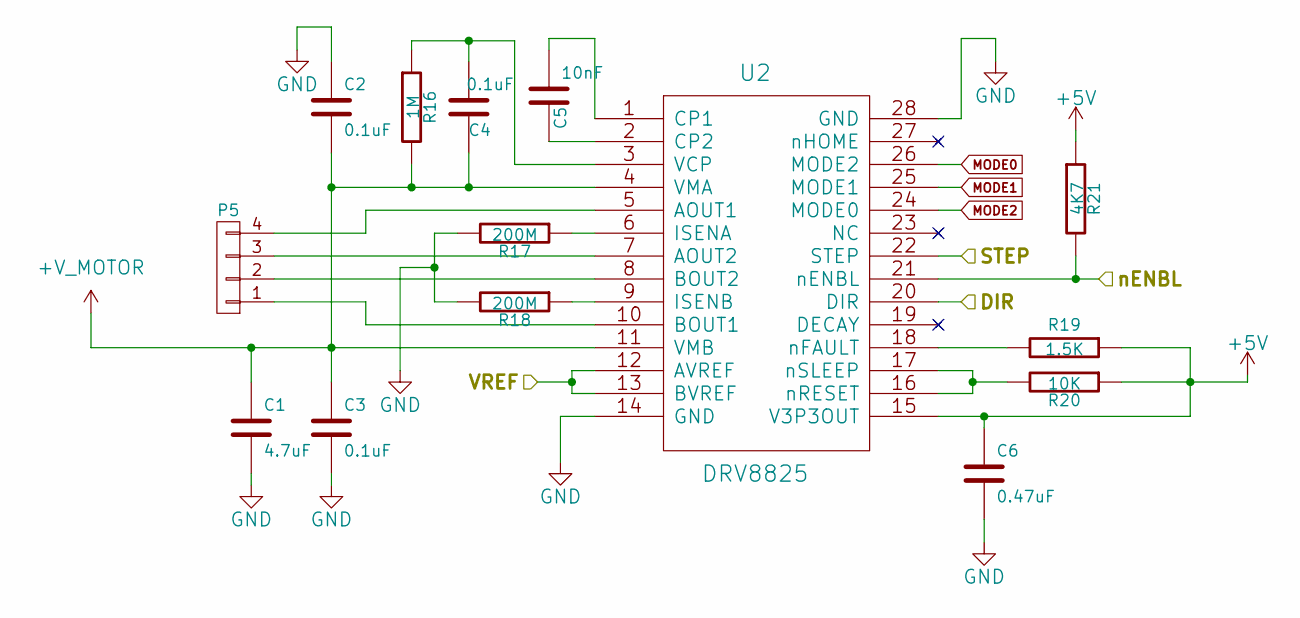
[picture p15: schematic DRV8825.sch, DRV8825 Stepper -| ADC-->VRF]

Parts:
C1: 4.7uF; C_0805_HandSoldering
C2, C3, C4: 0.1uF; C_0805_HandSoldering
C5: 10nF; C_0805_HandSoldering
C6: 0.47uF; C_0805_HandSoldering
P5: CONN_01X04; Socket_Strip_Straight_1x04
R16: 1M; R_0805_HandSoldering
R17, R18: 200M; R_0805_HandSoldering
R19: 1.5K; R_0805_HandSoldering
R20: 10K; R_0805_HandSoldering
R21: 4K7; R_0805_HandSoldering
U2: DRV8825; SOJ-32

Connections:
+5V: C6.1, R19.1, R20.1, R21.1, U2.15 (V3P3OUT); also elsewhere on the board
+V_MOTOR: C1.1, C2.2, C3.1, C4.1, R16.2, U2.4 (VMA), U2.11 (VMB); also elsewhere on the board
/DRV8825 X AXIS Stepper/VREF: U2.12 (AVREF), U2.13 (BVREF); also elsewhere on the board
MODE0: U2.26 (MODE2); also elsewhere on the board
MODE1: U2.25 (MODE1); also elsewhere on the board
MODE2: U2.24 (MODE0); also elsewhere on the board
unnamed: C4.2, R16.1, U2.3 (VCP)
unnamed: C5.1, U2.1 (CP1)
unnamed: C5.2, U2.2 (CP2)
unnamed: P5.1, U2.10 (BOUT1)
unnamed: P5.2, U2.8 (BOUT2)
unnamed: P5.3, U2.7 (AOUT2)
unnamed: P5.4, U2.5 (AOUT1)
unnamed: R17.1, U2.6 (ISENA)
unnamed: R18.1, U2.9 (ISENB)
unnamed: R19.2, U2.18 (nFAULT)
unnamed: R20.2, U2.16 (nRESET), U2.17 (nSLEEP)
X_DIR: U2.20 (DIR); also elsewhere on the board
X_ENABLE: R21.2, U2.21 (nENBL); also elsewhere on the board
X_STEP: U2.22 (STEP); also elsewhere on the board

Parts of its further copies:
C7, C13, C19: 4.7uF; C_0805_HandSoldering
C8, C9, C10, C14, C15, C16, C20, C21, C22: 0.1uF; C_0805_HandSoldering
C11, C17, C23: 10nF; C_0805_HandSoldering
C12, C18, C24: 0.47uF; C_0805_HandSoldering
P11, P12, P13: CONN_01X04; Socket_Strip_Straight_1x04
R32, R38, R44: 1M; R_0805_HandSoldering
R33, R34, R39, R40, R45, R46: 200M; R_0805_HandSoldering
R35, R41, R47: 1.5K; R_0805_HandSoldering
R36, R42, R48: 10K; R_0805_HandSoldering
R37, R43, R49: 4K7; R_0805_HandSoldering
U5, U6, U7: DRV8825; SOJ-32

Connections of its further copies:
+5V: C12.1, C18.1, C24.1, R35.1, R36.1, R37.1, R41.1, R42.1, R43.1, R47.1, R48.1, R49.1, U5.15 (V3P3OUT), U6.15 (V3P3OUT), U7.15 (V3P3OUT); also elsewhere on the board
+V_MOTOR: C7.1, C8.2, C9.1, C10.1, C13.1, C14.2, C15.1, C16.1, C19.1, C20.2, C21.1, C22.1, R32.2, R38.2, R44.2, U5.4 (VMA), U5.11 (VMB), U6.4 (VMA), U6.11 (VMB), U7.4 (VMA), U7.11 (VMB); also elsewhere on the board
/DRV8825 E AXIS Stepper/VREF: U7.12 (AVREF), U7.13 (BVREF); also elsewhere on the board
/DRV8825 Y AXIS Stepper/VREF: U5.12 (AVREF), U5.13 (BVREF); also elsewhere on the board
/DRV8825 Z AXIS Stepper/VREF: U6.12 (AVREF), U6.13 (BVREF); also elsewhere on the board
E_DIR: U7.20 (DIR); also elsewhere on the board
E_ENABLE: R49.2, U7.21 (nENBL); also elsewhere on the board
E_STEP: U7.22 (STEP); also elsewhere on the board
MODE0: U5.26 (MODE2), U6.26 (MODE2), U7.26 (MODE2); also elsewhere on the board
MODE1: U5.25 (MODE1), U6.25 (MODE1), U7.25 (MODE1); also elsewhere on the board
MODE2: U5.24 (MODE0), U6.24 (MODE0), U7.24 (MODE0); also elsewhere on the board
unnamed: C10.2, R32.1, U5.3 (VCP)
unnamed: C11.1, U5.1 (CP1)
unnamed: C11.2, U5.2 (CP2)
unnamed: C16.2, R38.1, U6.3 (VCP)
unnamed: C17.1, U6.1 (CP1)
unnamed: C17.2, U6.2 (CP2)
unnamed: C22.2, R44.1, U7.3 (VCP)
unnamed: C23.1, U7.1 (CP1)
unnamed: C23.2, U7.2 (CP2)
unnamed: P11.1, U5.10 (BOUT1)
unnamed: P11.2, U5.8 (BOUT2)
unnamed: P11.3, U5.7 (AOUT2)
unnamed: P11.4, U5.5 (AOUT1)
unnamed: P12.1, U6.10 (BOUT1)
unnamed: P12.2, U6.8 (BOUT2)
unnamed: P12.3, U6.7 (AOUT2)
unnamed: P12.4, U6.5 (AOUT1)
unnamed: P13.1, U7.10 (BOUT1)
unnamed: P13.2, U7.8 (BOUT2)
unnamed: P13.3, U7.7 (AOUT2)
unnamed: P13.4, U7.5 (AOUT1)
unnamed: R33.1, U5.6 (ISENA)
unnamed: R34.1, U5.9 (ISENB)
unnamed: R35.2, U5.18 (nFAULT)
unnamed: R36.2, U5.16 (nRESET), U5.17 (nSLEEP)
unnamed: R39.1, U6.6 (ISENA)
unnamed: R40.1, U6.9 (ISENB)
unnamed: R41.2, U6.18 (nFAULT)
unnamed: R42.2, U6.16 (nRESET), U6.17 (nSLEEP)
unnamed: R45.1, U7.6 (ISENA)
unnamed: R46.1, U7.9 (ISENB)
unnamed: R47.2, U7.18 (nFAULT)
unnamed: R48.2, U7.16 (nRESET), U7.17 (nSLEEP)
Y_DIR: U5.20 (DIR); also elsewhere on the board
Y_ENABLE: R37.2, U5.21 (nENBL); also elsewhere on the board
Y_STEP: U5.22 (STEP); also elsewhere on the board
Z_DIR: U6.20 (DIR); also elsewhere on the board
Z_ENABLE: R43.2, U6.21 (nENBL); also elsewhere on the board
Z_STEP: U6.22 (STEP); also elsewhere on the board

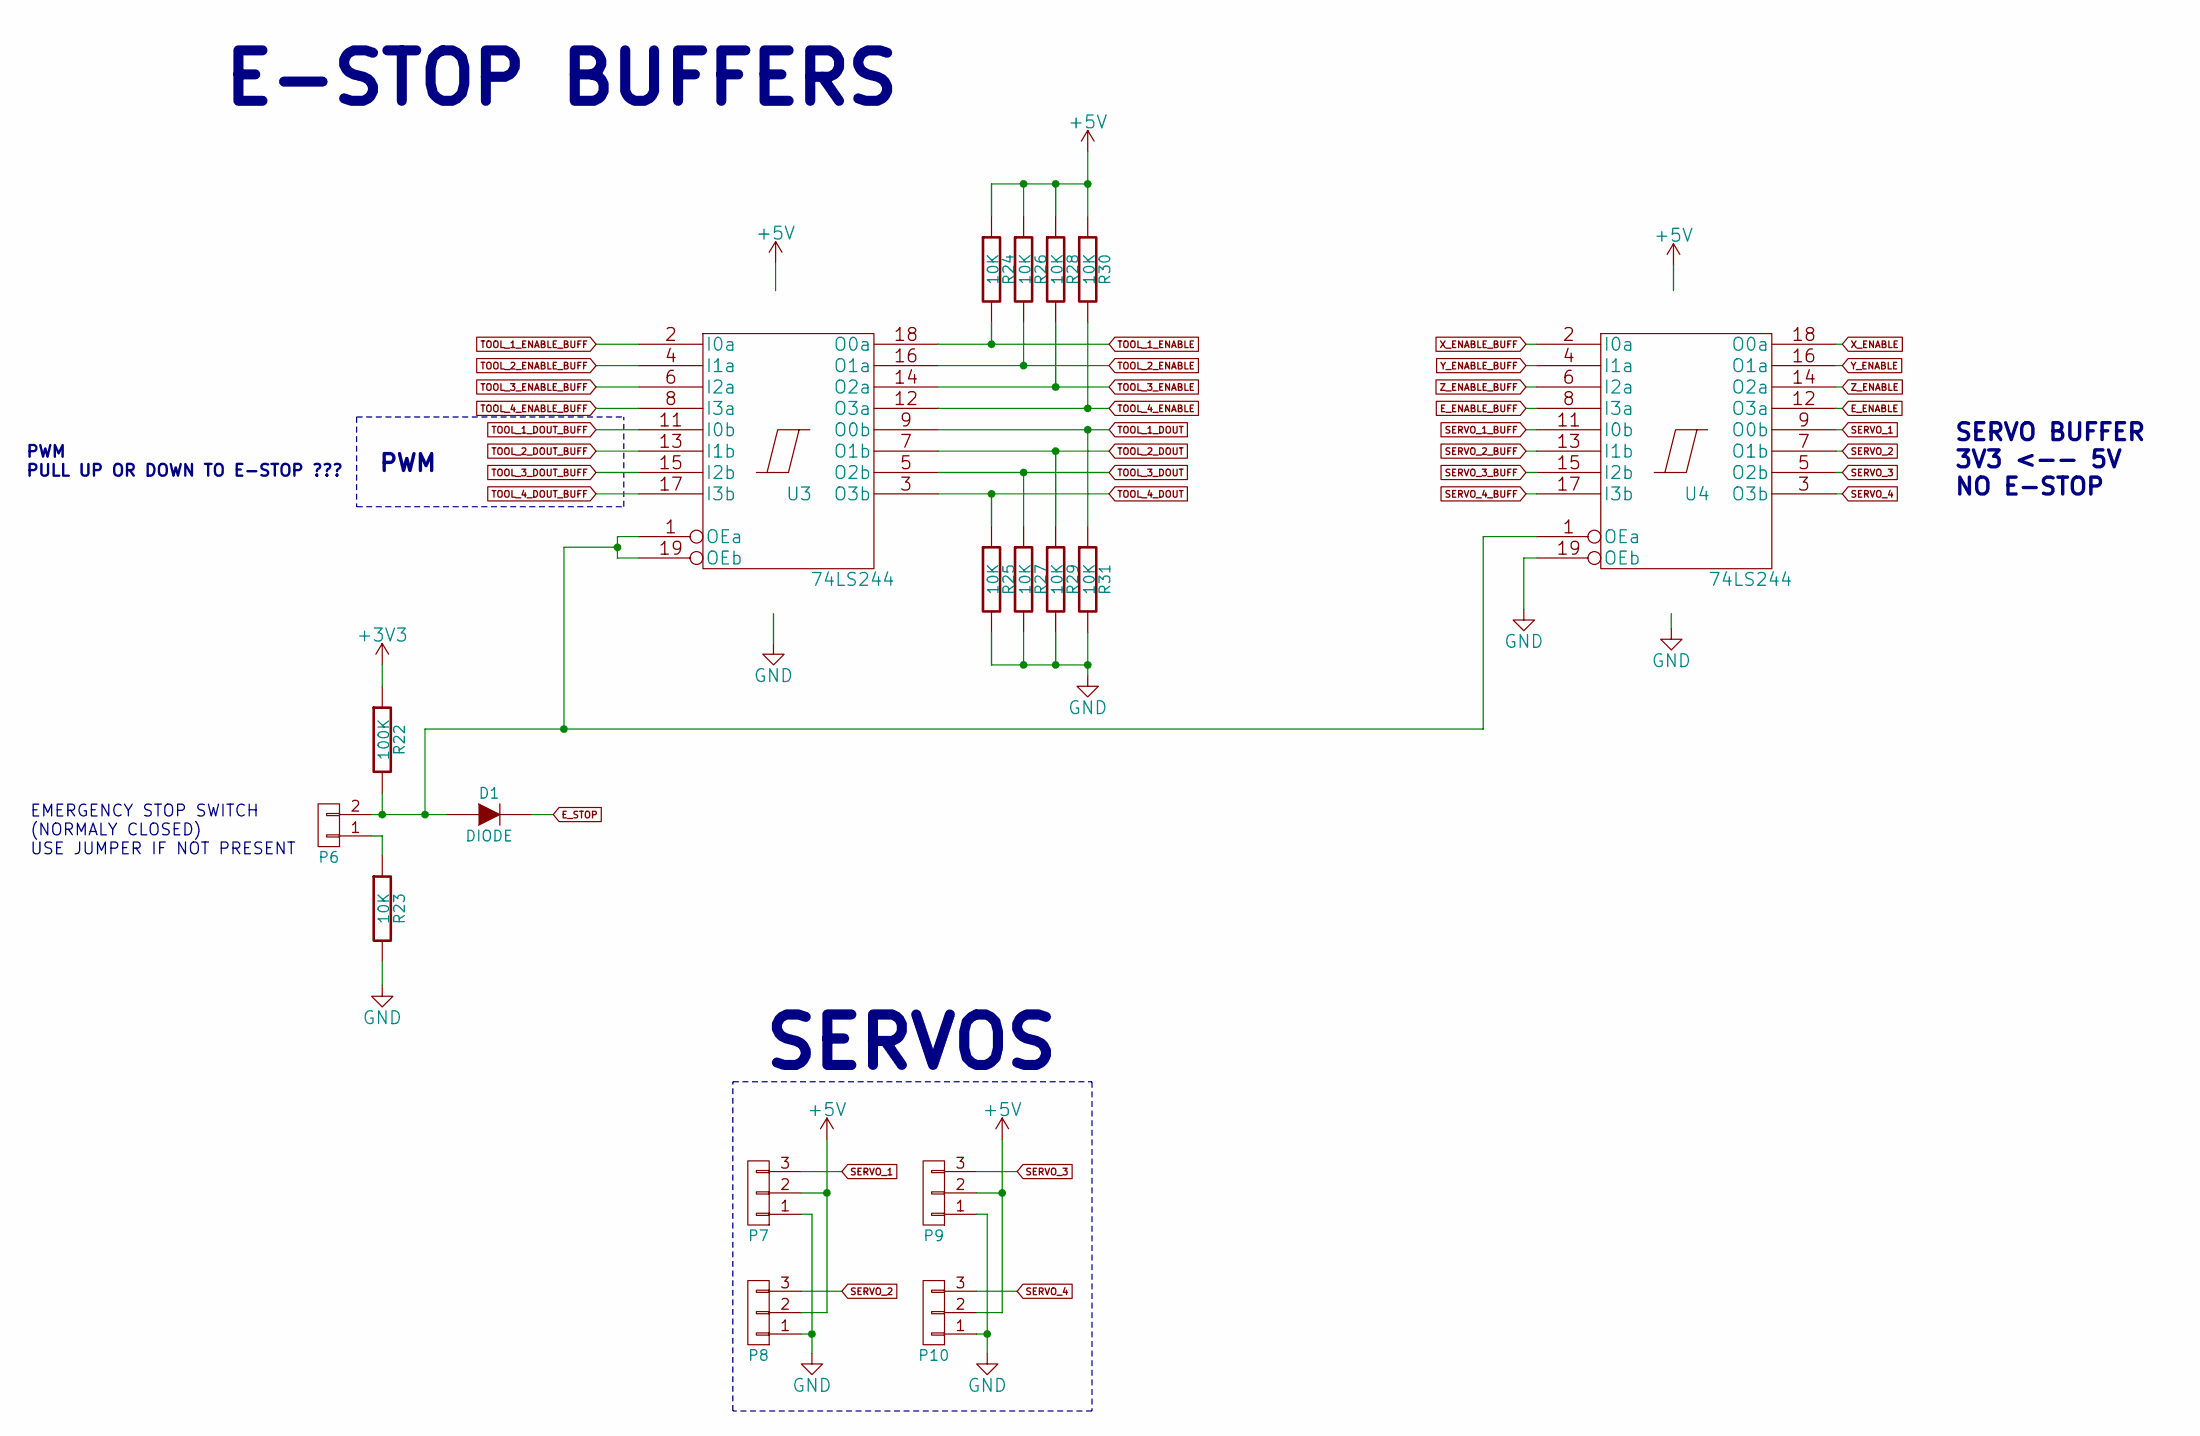
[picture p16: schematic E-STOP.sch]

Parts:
D1: DIODE
P6: CONN_01X02; Socket_Strip_Straight_1x02
P7, P8, P9, P10: CONN_01X03; Socket_Strip_Straight_1x03
R22: 100K; R_0805_HandSoldering
R23, R24, R25, R26, R27, R28, R29, R30, R31: 10K; R_0805_HandSoldering
U3, U4: 74LS244; SSOP-20

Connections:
+3V3: R22.1; also elsewhere on the board
+5V: P7.2, P8.2, P9.2, P10.2, R24.1, R26.1, R28.1, R30.1; also elsewhere on the board
E_ENABLE: U4.12 (O3a); also elsewhere on the board
E_ENABLE_BUFF: U4.8 (I3a); also elsewhere on the board
unnamed: D1.1 (A), P6.2, R22.2, U3.1 (OEa), U3.19 (OEb), U4.1 (OEa)
unnamed: P6.1, R23.1
SERVO_1: P7.3, U4.9 (O0b)
SERVO_1_BUFF: U4.11 (I0b); also elsewhere on the board
SERVO_2: P8.3, U4.7 (O1b)
SERVO_2_BUFF: U4.13 (I1b); also elsewhere on the board
SERVO_3: P9.3, U4.5 (O2b)
SERVO_3_BUFF: U4.15 (I2b); also elsewhere on the board
SERVO_4: P10.3, U4.3 (O3b)
SERVO_4_BUFF: U4.17 (I3b); also elsewhere on the board
TOOL_1_DOUT: R31.1, U3.9 (O0b); also elsewhere on the board
TOOL_1_DOUT_BUFF: U3.11 (I0b); also elsewhere on the board
TOOL_1_ENABLE: R24.2, U3.18 (O0a); also elsewhere on the board
TOOL_1_ENABLE_BUFF: U3.2 (I0a); also elsewhere on the board
TOOL_2_DOUT: R29.1, U3.7 (O1b); also elsewhere on the board
TOOL_2_DOUT_BUFF: U3.13 (I1b); also elsewhere on the board
TOOL_2_ENABLE: R26.2, U3.16 (O1a); also elsewhere on the board
TOOL_2_ENABLE_BUFF: U3.4 (I1a); also elsewhere on the board
TOOL_3_DOUT: R27.1, U3.5 (O2b); also elsewhere on the board
TOOL_3_DOUT_BUFF: U3.15 (I2b); also elsewhere on the board
TOOL_3_ENABLE: R28.2, U3.14 (O2a); also elsewhere on the board
TOOL_3_ENABLE_BUFF: U3.6 (I2a); also elsewhere on the board
TOOL_4_DOUT: R25.1, U3.3 (O3b); also elsewhere on the board
TOOL_4_DOUT_BUFF: U3.17 (I3b); also elsewhere on the board
TOOL_4_ENABLE: R30.2, U3.12 (O3a); also elsewhere on the board
TOOL_4_ENABLE_BUFF: U3.8 (I3a); also elsewhere on the board
VCC: U3.20 (VCC), U4.20 (VCC)
X_ENABLE: U4.18 (O0a); also elsewhere on the board
X_ENABLE_BUFF: U4.2 (I0a); also elsewhere on the board
Y_ENABLE: U4.16 (O1a); also elsewhere on the board
Y_ENABLE_BUFF: U4.4 (I1a); also elsewhere on the board
Z_ENABLE: U4.14 (O2a); also elsewhere on the board
Z_ENABLE_BUFF: U4.6 (I2a); also elsewhere on the board

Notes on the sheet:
EMERGENCY STOP SWITCH (NORMALY CLOSED) USE JUMPER IF NOT PRESENT
PWM
PWM PULL UP OR DOWN TO E-STOP ???
SERVO BUFFER 3V3 <-- 5V NO E-STOP
SERVOS
E-STOP BUFFERS

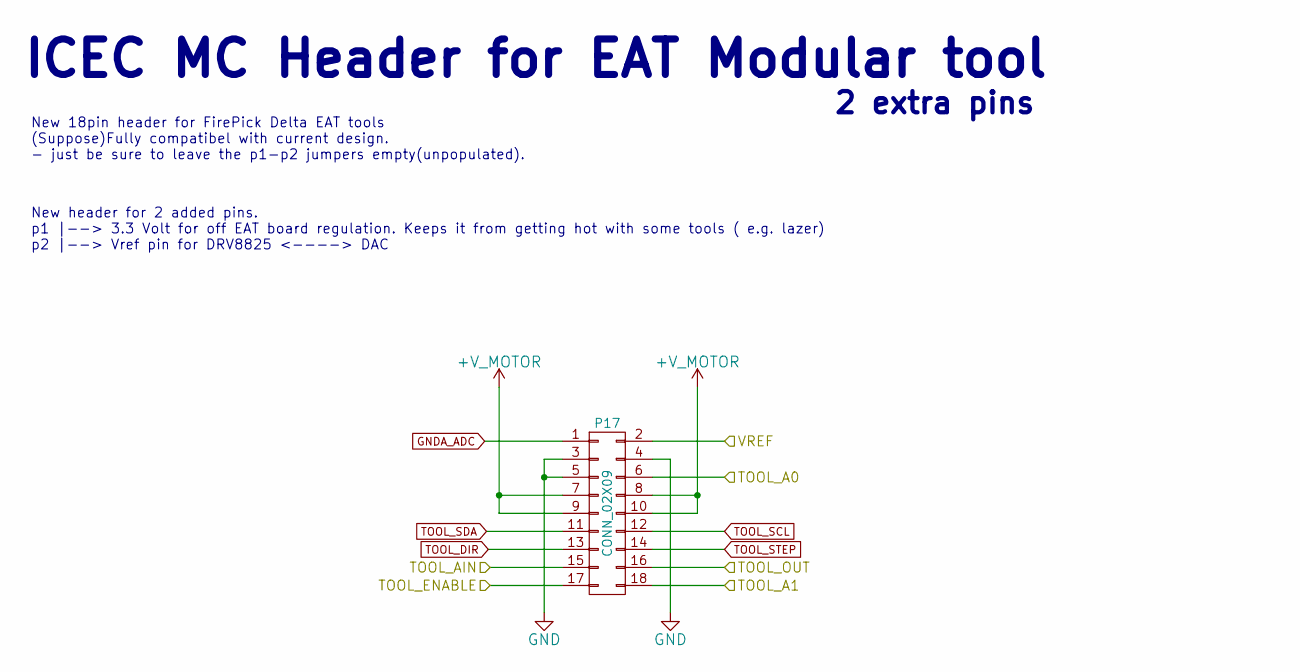
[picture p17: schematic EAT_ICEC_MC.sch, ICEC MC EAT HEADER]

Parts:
P14: CONN_02X09; Socket_Strip_Straight_2x09

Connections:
+V_MOTOR: P14.7, P14.8, P14.9, P14.10; also elsewhere on the board
/EAT_ICEC_MC_1/TOOL_A0: P14.6
/EAT_ICEC_MC_1/VREF: P14.2; also elsewhere on the board
GNDA_ADC: P14.1; also elsewhere on the board
TOOL_1_AIN: P14.15; also elsewhere on the board
TOOL_1_DOUT: P14.16; also elsewhere on the board
TOOL_1_ENABLE: P14.17; also elsewhere on the board
TOOL_DIR: P14.13; also elsewhere on the board
TOOL_SCL: P14.12; also elsewhere on the board
TOOL_SDA: P14.11; also elsewhere on the board
TOOL_STEP: P14.14; also elsewhere on the board

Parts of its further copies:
P15, P16, P17: CONN_02X09; Socket_Strip_Straight_2x09

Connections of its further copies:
+V_MOTOR: P15.7, P15.8, P15.9, P15.10, P16.7, P16.8, P16.9, P16.10, P17.7, P17.8, P17.9, P17.10; also elsewhere on the board
/EAT_ICEC_MC_2/TOOL_A1: P15.18
/EAT_ICEC_MC_2/VREF: P15.2; also elsewhere on the board
/EAT_ICEC_MC_3/VREF: P16.2; also elsewhere on the board
/EAT_ICEC_MC_4/TOOL_A0: P17.6
/EAT_ICEC_MC_4/TOOL_A1: P17.18
/EAT_ICEC_MC_4/VREF: P17.2; also elsewhere on the board
GNDA_ADC: P15.1, P16.1, P17.1; also elsewhere on the board
TOOL_2_AIN: P15.15; also elsewhere on the board
TOOL_2_DOUT: P15.16; also elsewhere on the board
TOOL_2_ENABLE: P15.17; also elsewhere on the board
TOOL_3_AIN: P16.15; also elsewhere on the board
TOOL_3_DOUT: P16.16; also elsewhere on the board
TOOL_3_ENABLE: P16.17; also elsewhere on the board
TOOL_4_AIN: P17.15; also elsewhere on the board
TOOL_4_DOUT: P17.16; also elsewhere on the board
TOOL_4_ENABLE: P17.17; also elsewhere on the board
TOOL_DIR: P15.13, P16.13, P17.13; also elsewhere on the board
TOOL_SCL: P15.12, P16.12, P17.12; also elsewhere on the board
TOOL_SDA: P15.11, P16.11, P17.11; also elsewhere on the board
TOOL_STEP: P15.14, P16.14, P17.14; also elsewhere on the board

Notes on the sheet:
New 18pin header for FirePick Delta EAT tools (Suppose)Fully compatibel with current design. - just be sure to leave the p1-p2 jumpers empty(unpopulated).
New header for 2 added pins. p1 |--> 3.3 Volt for off EAT board regulation. Keeps it from getting hot with some tools ( e.g. lazer) p2 |--> Vref pin for DRV8825 <----> DAC
ICEC MC Header for EAT Modular tool
2 extra pins

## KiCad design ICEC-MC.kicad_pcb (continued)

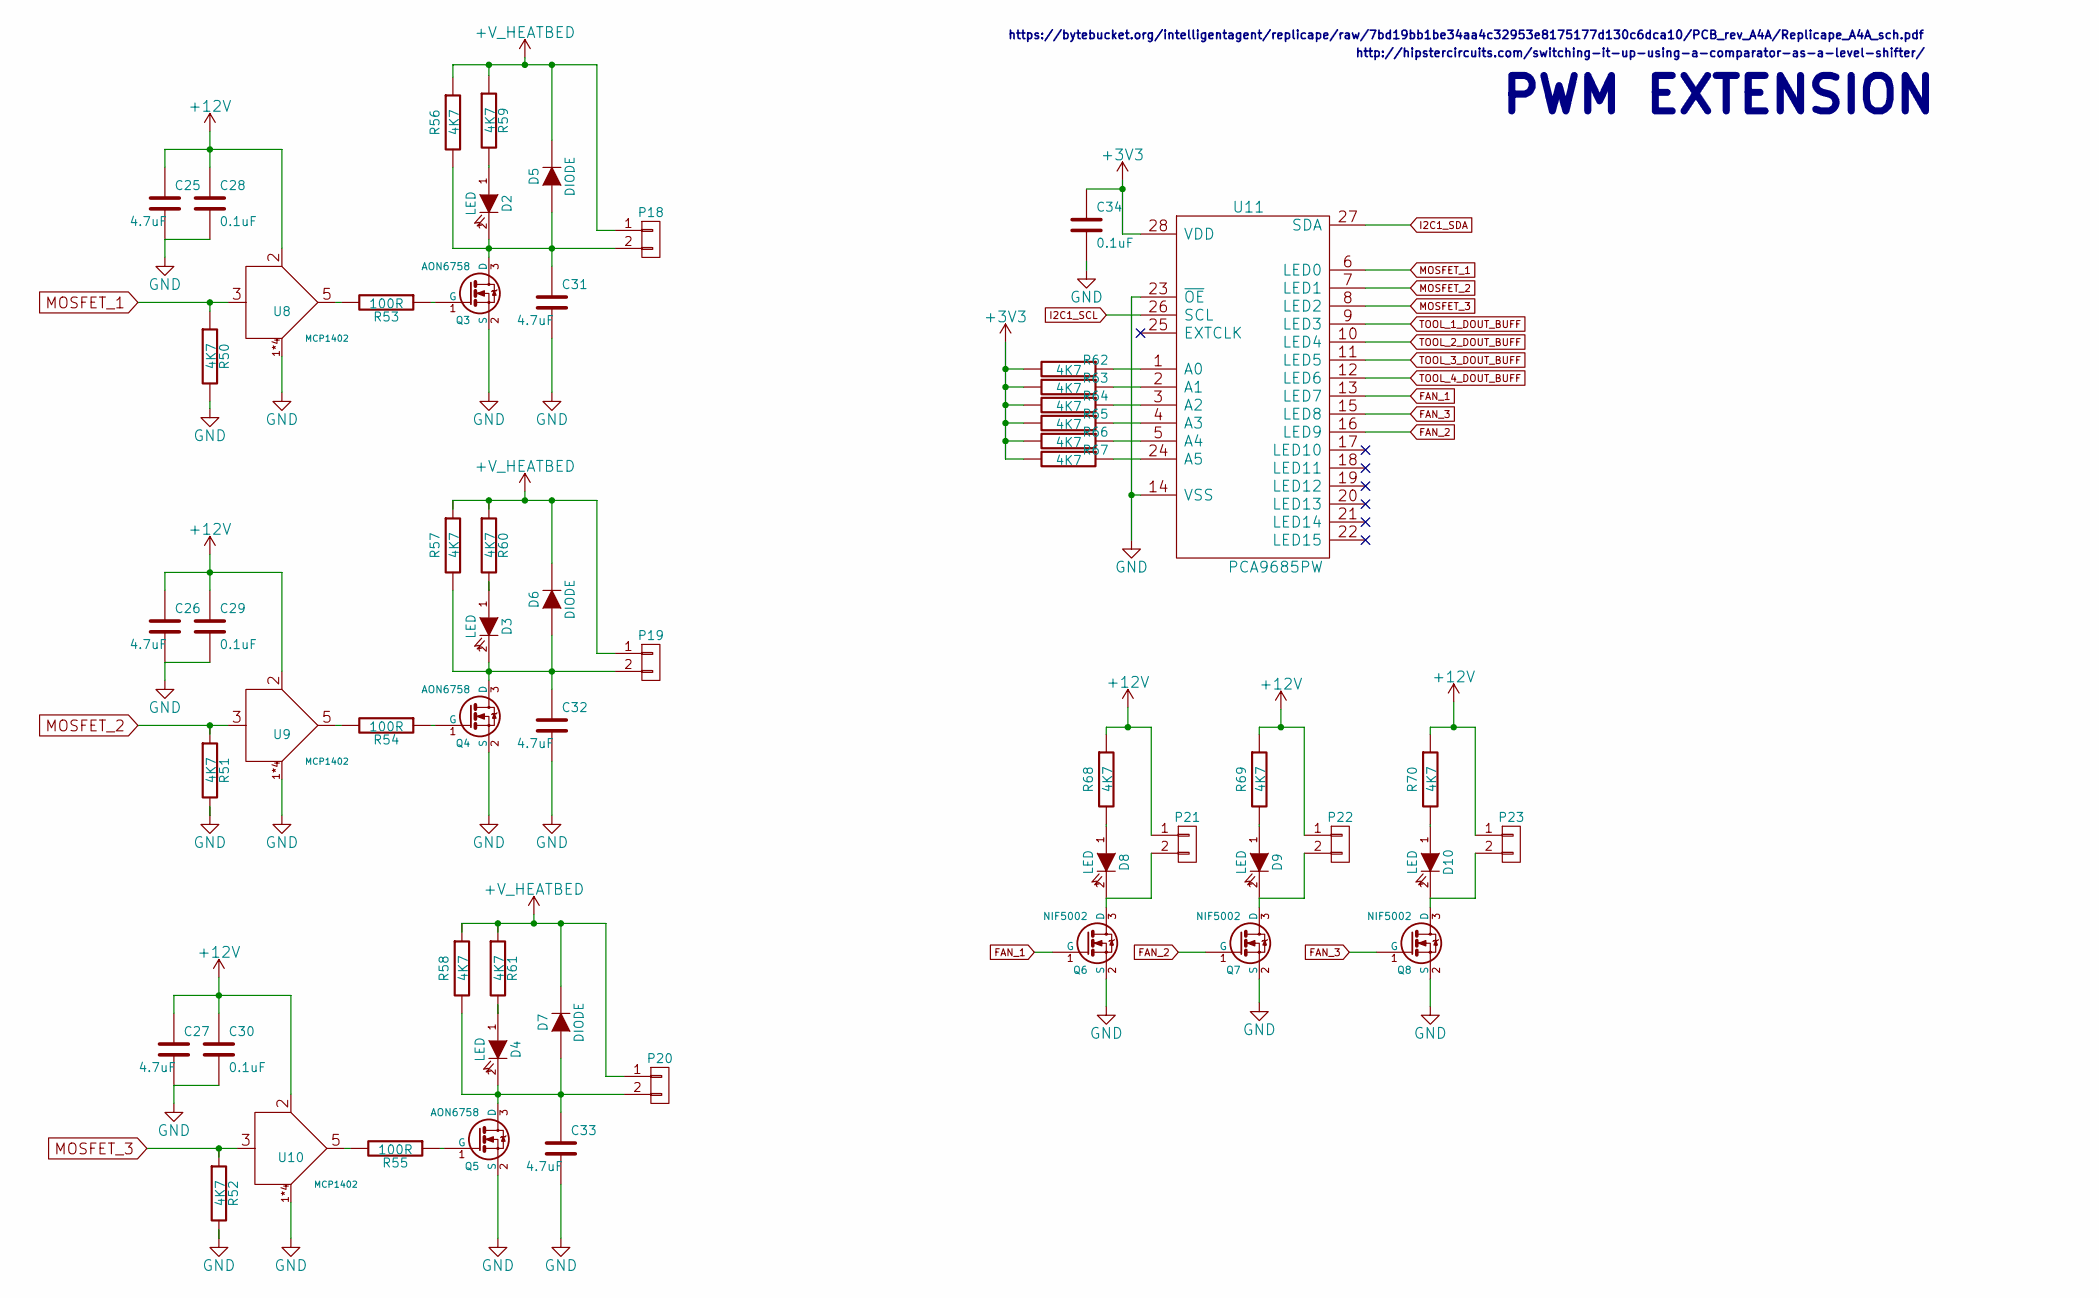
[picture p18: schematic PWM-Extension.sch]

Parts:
C25, C26, C27, C31, C32, C33: 4.7uF; C_0805_HandSoldering
C28, C29, C30, C34: 0.1uF; C_0805_HandSoldering
D2, D3, D4, D9, D10: LED; LED-0603
D5, D6, D7: DIODE
D8: LED; LED-0603; DigiKey 475-2816-1-ND
P18, P19, P20, P21, P22, P23: CONN_01X02; Socket_Strip_Straight_1x02
Q3, Q4, Q5: AON6758
Q6, Q7, Q8: NIF5002
R50, R51, R52, R56, R57, R58, R59, R60, R61, R62, R63, R64, R65, R66, R67, R68, R69, R70: 4K7; R_0805_HandSoldering
R53, R54, R55: 100R; R_0805_HandSoldering
U8, U9, U10: MCP1402
U11: PCA9685PW; TSSOP-28_4.4x9.7mm_Pitch0.65mm

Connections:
+3V3: C34.1, R62.2, R63.2, R64.2, R65.2, R66.2, R67.2, U11.28 (VDD); also elsewhere on the board
FAN_1: Q6.1 (G), U11.13 (LED7)
FAN_2: Q7.1 (G), U11.16 (LED9)
FAN_3: Q8.1 (G), U11.15 (LED8)
I2C1_SCL: U11.26 (SCL); also elsewhere on the board
I2C1_SDA: U11.27 (SDA); also elsewhere on the board
MOSFET_1: R50.1, U8.3, U11.6 (LED0)
MOSFET_2: R51.1, U9.3, U11.7 (LED1)
MOSFET_3: R52.1, U10.3, U11.8 (LED2)
unnamed: C31.1, D2.2 (K), D5.1 (A), P18.2, Q3.3 (D), R56.2
unnamed: C32.1, D3.2 (K), D6.1 (A), P19.2, Q4.3 (D), R57.2
unnamed: C33.1, D4.2 (K), D7.1 (A), P20.2, Q5.3 (D), R58.2
unnamed: D2.1 (A), R59.2
unnamed: D3.1 (A), R60.2
unnamed: D4.1 (A), R61.2
unnamed: D8.1 (A), R68.2
unnamed: D8.2 (K), P21.2, Q6.3 (D)
unnamed: D9.1 (A), R69.2
unnamed: D9.2 (K), P22.2, Q7.3 (D)
unnamed: D10.1 (A), R70.2
unnamed: D10.2 (K), P23.2, Q8.3 (D)
unnamed: Q3.1 (G), R53.1
unnamed: Q4.1 (G), R54.1
unnamed: Q5.1 (G), R55.1
unnamed: R53.2, U8.5
unnamed: R54.2, U9.5
unnamed: R55.2, U10.5
unnamed: R62.1, U11.1 (A0)
unnamed: R63.1, U11.2 (A1)
unnamed: R64.1, U11.3 (A2)
unnamed: R65.1, U11.4 (A3)
unnamed: R66.1, U11.5 (A4)
unnamed: R67.1, U11.24 (A5)
TOOL_1_DOUT_BUFF: U11.9 (LED3); also elsewhere on the board
TOOL_2_DOUT_BUFF: U11.10 (LED4); also elsewhere on the board
TOOL_3_DOUT_BUFF: U11.11 (LED5); also elsewhere on the board
TOOL_4_DOUT_BUFF: U11.12 (LED6); also elsewhere on the board

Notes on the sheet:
PWM EXTENSION
http://hipstercircuits.com/switching-it-up-using-a-comparator-as-a-level-shifter/
https://bytebucket.org/intelligentagent/replicape/raw/7bd19bb1be34aa4c32953e8175177d130c6dca10/PCB_rev_A4A/Replicape_A4A_sch.pdf

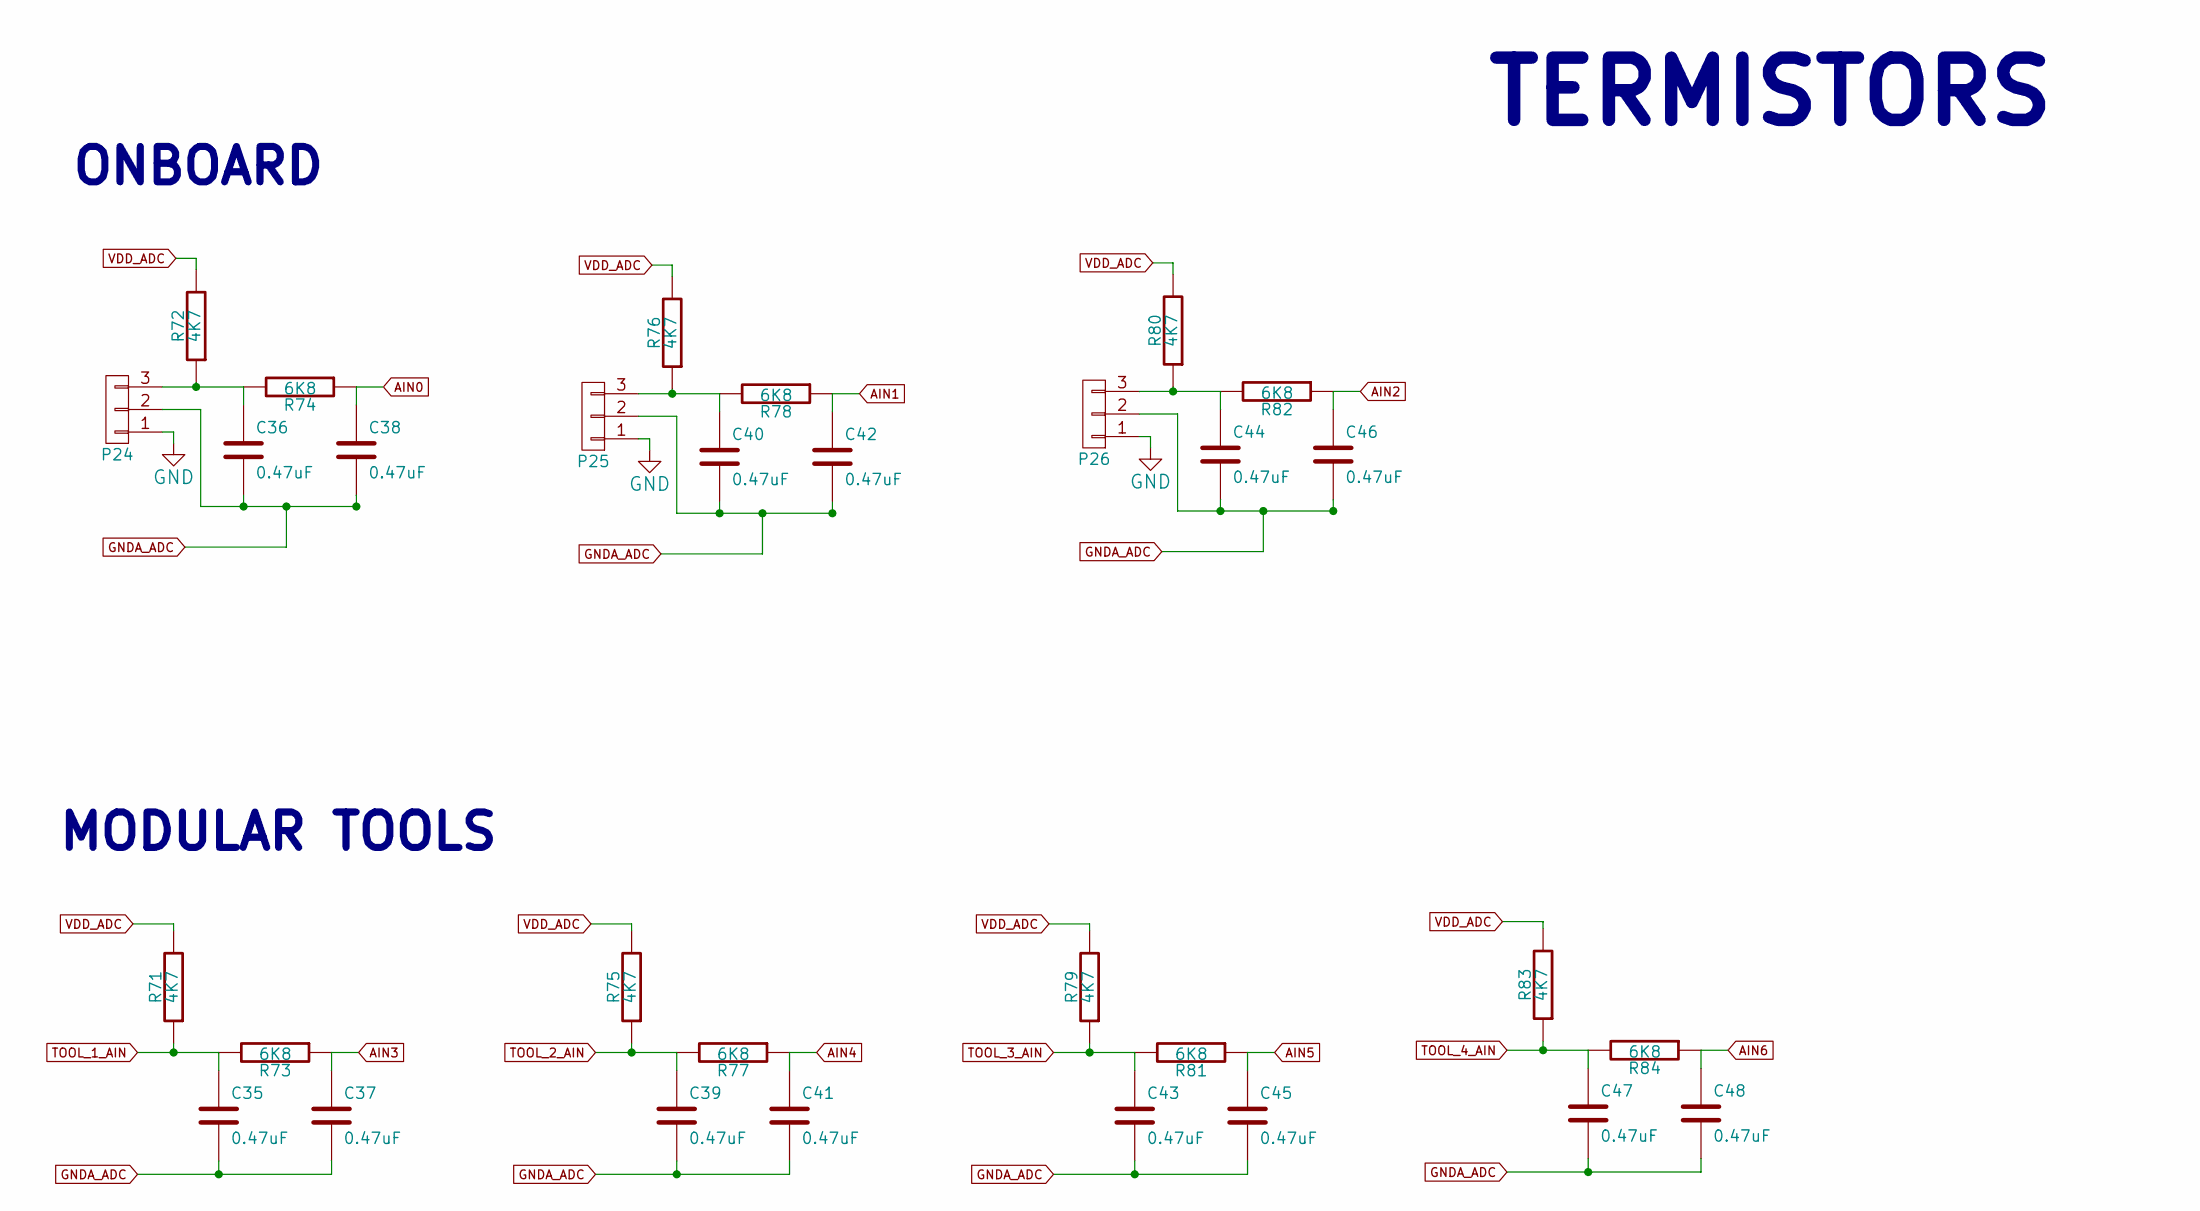
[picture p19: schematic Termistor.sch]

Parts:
C35, C36, C37, C38, C39, C40, C41, C42, C43, C44, C45, C46, C47, C48: 0.47uF; C_0805_HandSoldering
P24, P25, P26: CONN_01X03; Socket_Strip_Straight_1x03
R71, R72, R75, R76, R79, R80, R83: 4K7; R_0805_HandSoldering
R73, R74, R77, R78, R81, R82, R84: 6K8; R_0805_HandSoldering

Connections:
AIN0: C38.1, R74.1; also elsewhere on the board
AIN1: C42.1, R78.1; also elsewhere on the board
AIN2: C46.1, R82.1; also elsewhere on the board
AIN3: C37.1, R73.1; also elsewhere on the board
AIN4: C41.1, R77.1; also elsewhere on the board
AIN5: C45.1, R81.1; also elsewhere on the board
AIN6: C48.1, R84.1; also elsewhere on the board
GNDA_ADC: C35.2, C36.2, C37.2, C38.2, C39.2, C40.2, C41.2, C42.2, C43.2, C44.2, C45.2, C46.2, C47.2, C48.2, P24.2, P25.2, P26.2; also elsewhere on the board
unnamed: C36.1, P24.3, R72.1, R74.2
unnamed: C40.1, P25.3, R76.1, R78.2
unnamed: C44.1, P26.3, R80.1, R82.2
TOOL_1_AIN: C35.1, R71.1, R73.2; also elsewhere on the board
TOOL_2_AIN: C39.1, R75.1, R77.2; also elsewhere on the board
TOOL_3_AIN: C43.1, R79.1, R81.2; also elsewhere on the board
TOOL_4_AIN: C47.1, R83.1, R84.2; also elsewhere on the board
VDD_ADC: R71.2, R72.2, R75.2, R76.2, R79.2, R80.2, R83.2; also elsewhere on the board

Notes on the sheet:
TERMISTORS
ONBOARD
MODULAR TOOLS

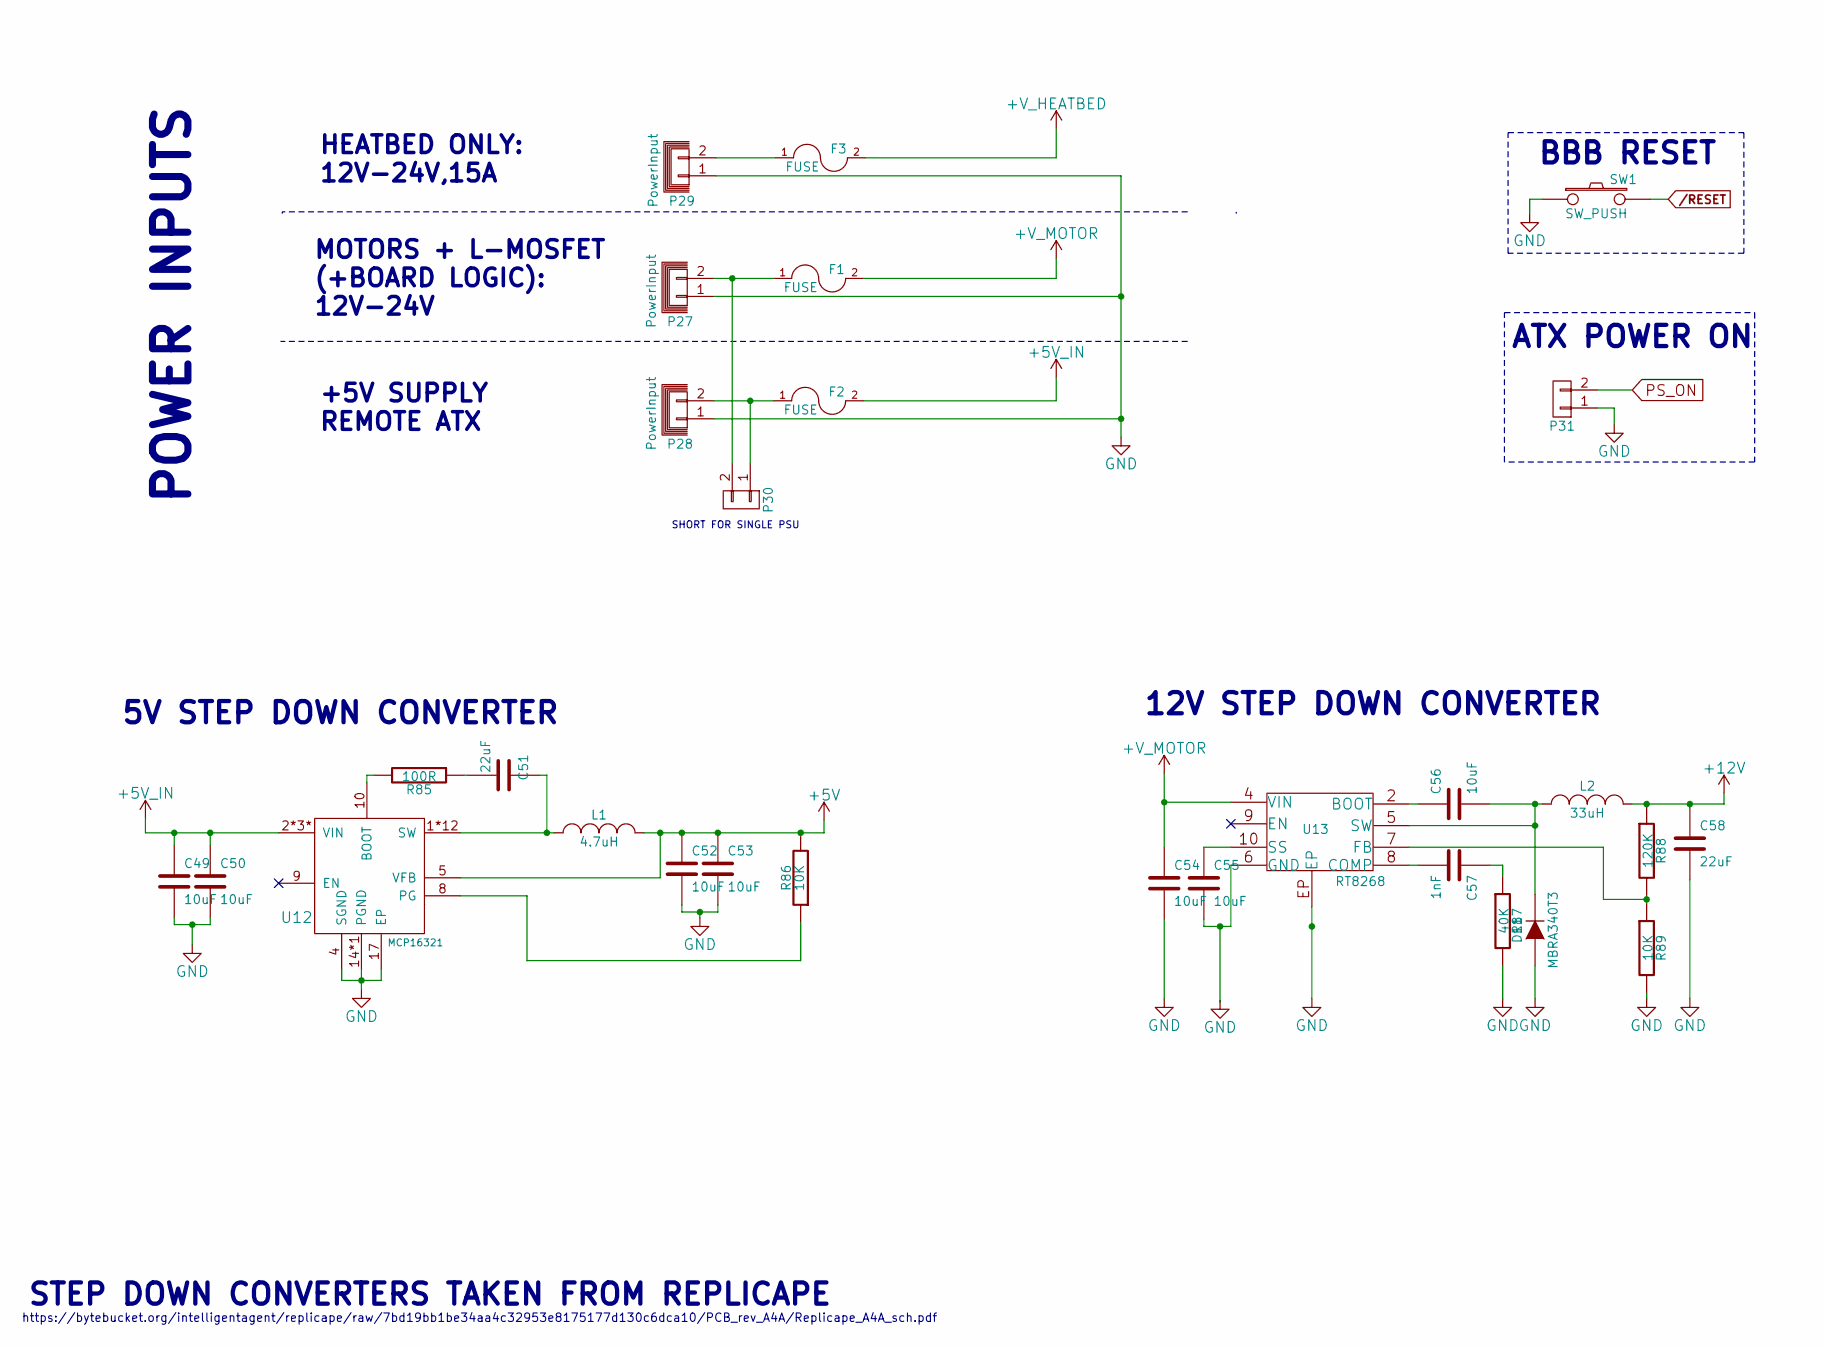
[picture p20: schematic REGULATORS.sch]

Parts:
C49, C50, C52, C53, C54, C55, C56: 10uF; C_0805_HandSoldering
C51, C58: 22uF; C_0805_HandSoldering
C57: 1nF; C_0805_HandSoldering
D11: MBRA340T3
F1, F2, F3: FUSE
L1: 4.7uH
L2: 33uH
P27, P28, P29: PowerInput; Socket_Strip_Straight_1x02
P30, P31: CONN_01X02; Socket_Strip_Straight_1x02
R85: 100R; R_0805_HandSoldering
R86, R89: 10K; R_0805_HandSoldering
R87: 40K; R_0805_HandSoldering
R88: 120K; R_0805_HandSoldering
SW1: SW_PUSH
U12: MCP16321
U13: RT8268

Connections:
+5V: C52.1, C53.1, L1.2, R86.2, U12.5 (VFB); also elsewhere on the board
+5VD: C49.1, C50.1, F2.2, U12.2*3* (VIN)
+V_MOTOR: C54.1, F1.2, U13.4 (VIN); also elsewhere on the board
unnamed: C51.1, L1.1, U12.1*12 (SW)
unnamed: C51.2, R85.1
unnamed: C55.1, U13.10 (SS)
unnamed: C56.1, U13.2 (BOOT)
unnamed: C56.2, D11.2 (K), L2.1, U13.5 (SW)
unnamed: C57.1, R87.1
unnamed: C57.2, U13.8 (COMP)
unnamed: F1.1, P27.2, P30.2
unnamed: F2.1, P28.2, P30.1
unnamed: F3.1, P29.2
unnamed: R85.2, U12.10 (BOOT)
unnamed: R86.1, U12.8 (PG)
unnamed: R88.2, R89.1, U13.7 (FB)
PS_ON: P31.2; also elsewhere on the board

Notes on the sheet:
ATX POWER ON
SHORT FOR SINGLE PSU
HEATBED ONLY: 12V-24V,15A
MOTORS + L-MOSFET (+BOARD LOGIC): 12V-24V
+5V SUPPLY REMOTE ATX
POWER INPUTS
BBB RESET
5V STEP DOWN CONVERTER
https://bytebucket.org/intelligentagent/replicape/raw/7bd19bb1be34aa4c32953e8175177d130c6dca10/PCB_rev_A4A/Replicape_A4A_sch.pdf
STEP DOWN CONVERTERS TAKEN FROM REPLICAPE
12V STEP DOWN CONVERTER

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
Board: 2 copper layers, 202 parts (2 on the bottom side), 186 nets, no tracks yet.

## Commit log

2015-02-16 first release
    [DRV8825.sch, E-STOP.sch, EAT_ICEC_MC.sch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]
2015-02-18 Add Some Info about project
    [DRV8825.sch, E-STOP.sch, EAT_ICEC_MC.sch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]
